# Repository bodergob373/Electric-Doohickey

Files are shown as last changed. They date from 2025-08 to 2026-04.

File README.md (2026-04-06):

# Electric-Doohickey

## Description
A custom go-kart powered by 6 Nissan Leaf battery modules in series. It is driven by two hoverboard motors. The throttle sends signals to a microcontroller, which sends adjusted signals to both motor controllers. The rear wheels are on a suspension arm 

## Why?
My main goal for the future is to build an ethanol-electric hybrid car from scratch. To do this, I need real-world experience designing electrical and mechanical stuff and more practice welding. I'm making this project so that I can design the electric part of the hybrid car and test it on a small, fast, and fun vehicle with only half the number of batteries, motor controllers, and motors.

## The Build
https://github.com/user-attachments/assets/639fb712-8df2-44af-8d2e-14ca03924510





## Model




## Wiring Diagram


### 3D Printed Parts for Mounting the Twist Throttle and Hoverboard Motor


### Hoverboard Motor Connected with 3D-Printed Mount


### BOM:

| Part | Purpose | Amount | Cost |
|---|---|---|---|
| Curved and straight metal tubes | Frame | 4 curved, 6 straight | $0.00  |
| Extension springs | Rear suspension | 4 | $0.00  |
| Plastic chair | Seat | 1 | $0.00  |
| 10" tires | Front wheel and stabilizers | 3 | $0.00  |
| Hoverboard motor | Rear wheels | 2 | $0.00  |
| ESP32 | Send throttle input to both controllers | 1 | $0.00  |
| 2S LiPo battery | Power microcontroller and contactor | 1 | $0.00  |
| Switch | Connect small battery to microcontroller and contactor | 1 | $0.00  |
| 3/4" x 24" threaded rod | Hold suspension arm | 1 | $10.51 |
| 5/16" x 72" threaded rod | Hold battery modules | 1 | $7.57  |
| 5/8" x 12" threaded rod | Hold front wheel and springs | 1 | $4.34  |
| 5/8" x 36" threaded rod | Axle for stabilizing wheels | 1 | $11.31 |
| 1/2" x 36" threaded rod | Steering rod | 1 | $7.93  |
| Used 2nd-gen Nissan Leaf battery modules | Power motors | 6 | $80.00 |
| Twist throttle | Throttle | 1 | $4.94  |
| Motor controllers | Control motors | 2 | $120.00|
| 135A contactor | Connect battery to motor controllers when turned on | 1 | $14.29 |
| 0.25" x 1" x 72" aluminum flat bar | Bus-bars for battery power terminals | 2 | $18.72 |
| 20mm M6 bolts | Connect power terminals to bus-bars | 30 | $8.07  |
| 100 ft 20 AWG silicone wire | Connect to throttle and contactor | 100 ft | $13.98 |
| 1/4" ring terminals | Connect to throttle and contactor | 100 | $8.99  |
| 20 ft 8 AWG silicone wire | Connect motor controller to battery and motors | 20 ft | $19.99 |
| 1/2" shaft collars | Hold parts on steering rod | 10 | $8.49  |
| 5/8" shaft collars | Hold wheel nuts in place | 10 | $8.49  |
| 3/4" shaft collars | Hold suspension arm in place | 8 | $13.99 |
| Misc screws, nuts, and washers | Attach wheels, springs, steering, throttle  | ~20 | $10.00 |
| | **Total** | | **$371.61** |

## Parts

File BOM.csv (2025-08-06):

Part | Purpose | Amount | Cost | Notes
curved and straight metal tubes | frame | 4 curved, 6 straight | 0 | scrap trampoline parts
extension springs | rear suspension | 4 | 0 | scrap trampoline parts
plastic chair | seat | 1 | 0 | already have
10" tires | front wheel and stabilizers | 3 | 0 | already have
hoverboard motor | rear wheels | 2 | 0 | already have
esp32 | send throttle input to both controllers | 1 | 0 | already have
2s lipo battery | power microcontroller and contactor | 1 | 0 | already have
switch | connect small battery to microcontroller and contactor | 1 | 0 | already have
3/4" x 24" threaded rod | hold suspension arm | 1 | 10.51
5/16" x 72" threaded rod | hold battery modules | 1 | 7.57
5/8" x 12" threaded rod | hold front wheel and springs | 1 | 4.34
5/8" x 36" threaded rod | axle for stabilizing wheels | 1 | 11.31
1/2" x 36" threaded rod | steering rod | 1 | 7.93
used 2nd-gen nissan leaf battery modules | power motors | 6 | 80 | 30 modules were $400
twist throttle | throttle | 1 | 4.94
motor controllers | control motors | 2 | 120 | i've already bought the more expensive motor controllers for the old design. this is the price of the cheaper motor controllers i would have used for the new design.
135A contactor | connect battery to motor controllers when turned on | 1 | 14.29
0.25"x1"x72" aluminum flat bar | bus-bars for battery power terminals | 2 | 18.72
20mm m6 bolts | connect power terminals to bus-bars | 30 | 8.07
100 ft 20 AWG silicone wire | connect to throttle and contactor | 100 ft | 13.98
1/4" ring terminals | connect to throttle and contactor | 100 | 8.99
20 ft 8 AWG silicone wire | connect motor controller to battery and motors | 20 ft | 19.99
1/2" shaft collars | hold parts on steering rod | 10 | 8.49
5/8" shaft collars | hold wheel nuts in place | 10 | 8.49
3/4" shaft collars | hold suspension arm in place | 8 | 13.99
misc screws, nuts, and washers | attach wheels, springs, steering, throttle | ~20 | 10
 |  |  | Total
 |  |  | 371.61

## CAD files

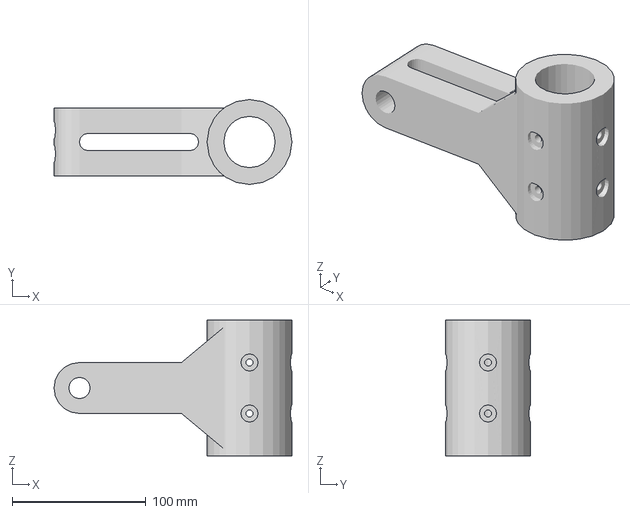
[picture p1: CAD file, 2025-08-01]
CAD/wheelmountprint.step
177.8 x 63.5 x 101.6 mm

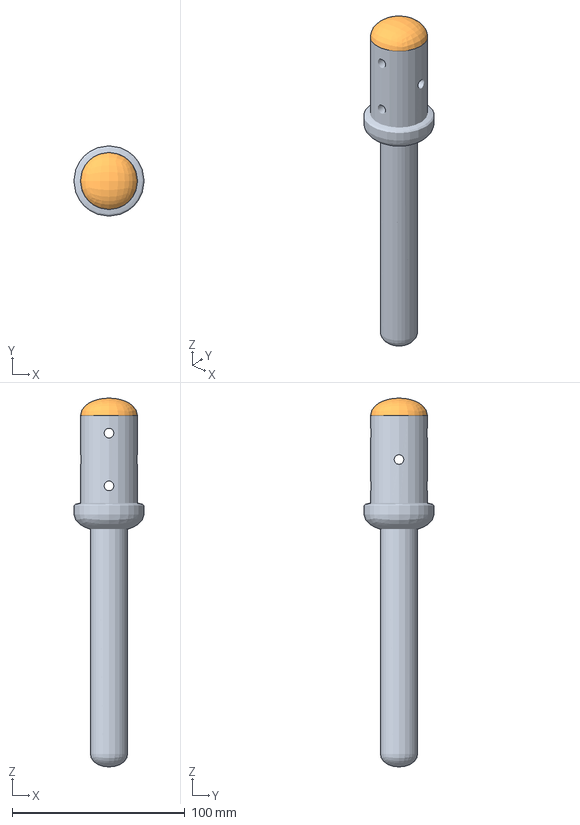
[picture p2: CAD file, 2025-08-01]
CAD/handlemountprint.step
40.6 x 40.6 x 213.4 mm

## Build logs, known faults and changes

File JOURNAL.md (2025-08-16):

---
title: Electric Doohickey
author: Jonathan Itoh
description: A custom go-kart powered by 6 Nissan Leaf battery modules. It is driven by two hoverboard motors. The throttle sends signals to a microcontroller, which sends adjusted signals to both motor controllers. The rear wheels are on a suspension arm.
created_at: 2025-06-25
---
**total time spent: 130h**

# June 25th: Research
In order to use one of the 12kW 72V hub motors that I want to use for the full car, I need powerful batteries. I looked at battery cells to buy, but I would need a lot of them. They're expensive and I don't want to wire them all together, so I searched for used EV/hybrid batteries. I found listings for battery modules from both a Toyota Prius and Nissan Leaf. I decided to use the Leaf batteries because they're cheaper and more commonly used.

module-from-nissan-leaf-gen-2-24kwh

**Total time spent: 4h**

# June 26th: Research 2
I thought that because they're from a car, maybe I could only use one module with smaller motors. After researching the nominal voltage, I would need more because they're only 8.4V. If I want to keep using the powerful motor, I would need 9 modules. It turns out that their nominal voltage is around 7.2V, so I would actually need 10 in series. The battery also needs to supply enough current for the motor. 12000kW / 72V is 167A, so I will need more battery modules in parallel. I chose to have 4 modules in parallel for the full car with 2 motors, so this kart with only 1 motor should only have 2 in parallel. It's still not enough to run at 12kW continuously, but it could maybe supply enough for a few seconds during acceleration.



**Total time spent: 3h**

# June 28th: Research 3
I found the motor controller. It's liquid-cooled and can handle 150A continuous at 72V. I researched parts of a liquid cooling system, but I realized it probably won't be using too much continuous current.

**Total time spent: 3h**

# June 28th: Batteries
I bought 30 Nissan Leaf batteries and made sure they worked.



**Total time spent: 3h**

# July 1st: Metal
I looked around for scrap pipes and found curved segments of an old trampoline frame. I tore it apart, measured the segments, set up the 3D workspace, and modeled them. I had a hard time modeling the curve so I measured the pipe's length, made a circle with a circumference 12 times that, and got a 12th segment. Because they're curved, an oval frame would be simple.



**Total time spent: 5h**

# July 2nd: Designing
I measured parts the 10" wheels and modeled them. I also got their inner diameter and found that Home Depot had perfect 5/8" threaded rods. Then, I measured the battery modules, double checked them with online dimensions, and modeled them. I looked at how batteries are usually wired in series and parallel and made the 10S2p design with the battery modules.



**Total time spent: 3h**

# July 3rd: Designing 2
Using bus bars that go across the batteries in a straight line would be simpler, so I rotated every other parallel group and added bus bars. For the kart, I decided to use 4 curved segments in an oval. For simplicity, the steering is only 1 wheel. It's not a bike so I put the other wheels on the sides to keep it upright. I designed the fork, arranged the frame quarters, positioned the seat and steering, added foot bars, designed the battery frame, and put the side wheels at an angle.




**Total time spent: 4h**

# July 4th: Research 4
Found crimp terminals for connecting the motor to the motor controller. I started researching what BMS I need. Only one voltage-sensing lead is needed per parallel group, so I would need a 10S BMS that can handle high amps. Many people use Orion BMS, but they're $400-$800. I spent a while lookimg for BMS units on Aliexpress and couldn't find many. I also wasn't completely sure whether I actually need only one for the whole battery pack or one per series string. The only one I found that might work could be an ANT BMS.

ANT-BMS-10S-24S-50A-180A-Smart-32V-88V-Lifepo4-li-ion-LTO-Battery-Protection-Board-Double-PCBA-2
71Gar08qu2L _SX522_

**Total time spent: 5h**

# July 5th: Research 5
I realized that the Nissan Leaf modules each have 4 cells in a 2S2P configuration, so a 10S BMS wouldn't even work well. I also found out that the mysterious third terminal between the positive and negative terminals is due to the 2S and is required for voltage sensing. So instead, I will need a 20S BMS. I searched Aliexpress again and found a company that has many different BMS units and found a 25S BMS. I went back to Aliexpress and searched for the same model and found a slightly cheaper one. The BMS requires outside charge, discharge, and pre-charge contactors. I found a 500A contactor.

**Total time spent: 4h**

# July 6th: Research 6
Apparently, another motor controller from the same company is both better and $60 cheaper than the one I already found, so I will use that. The pre-charge contactor does not need to handle as much current, so I found a smaller and cheaper contactor. The 500A contactors I found disappeared so I will use ones that the BMS seller also has. The wiring diagram in the BMS manual also shows that a pre-charge resitor is needed. I calculated the required resistance and found a chassis-mount resistor that can handle the current. I also calculated the cross-sectional area of copper I need for the bus bars on the positive and negative terminals. The bus bars for the voltage-sensing terminals only need to be cheap and wide enough to bolt onto the terminals. I was able to find enough copper at good sizes for a decent price. Then, I found M4 and M6 brass bolts and screws for the battery terminals. For wiring, I found 20 AWG silicone wire for voltage sensing and 8 AWG silicone wire for the motor controller. 2/0 AWG silicone wire is way too expensive.





**Total time spent: 6h**

# July 7th: Designing 3
I modeled the motor controller.



**Total time spent: 0.5h**

# July 9th: Designing 4
To simplify battery mounting and wiring, I put all the batteries in one stack supported by threaded rods on three crosspipes of the frame. I also modeled the BMS, shunt resistor, both contactor sizes, the hub motor, and the twist throttle. To fit the twist throttle to the pipe, I designed a 3D printable adapter that it could fit around. Then, I added angled pipes to connect the stabilizers to the frame. For the rear wheel, I would need a strong way to mount the hub motor on the frame, but that would result in gross angles between the mounting pipes and the curved sides of the frame. I used this as an opportunity to add a swing arm with nice 90 degree angles connected to the frame with a threaded rod, holes, and nuts. For suspension, I put leftover trampoline extension springs under the swing arm so that they would stretch when the suspension is compressed. Finally, I started the wiring design by connecting the motor controller to the hub motor.





**Total time spent: 9h**

# July 10th: Designing 5
I modeled the pre-charge resistor and designed all the wiring. To strengthen the stabilizers and make them easier to build, I removed their tilt and put them both on a threaded rod. I also designed the steering to actually work by havoing a pipe that rotates inside another and supports the lower half of the fork. A threaded rod connects it to the handle with nuts and shaft collars. Because I can't buy the $700 hub motor now, I want to use a hoverboard wheel temporarily because the voltage and current limits of the motor controller can be set. So that I can keep all the metal parts the same, I designed a 3D printable mount that allows the hoverboard wheel to be attached to the swing arm lower down. 





**Total time spent: 7h**

# July 11th: Part Sourcing
I continued looking for parts such as wires and terminals. I would need 2/0 or 1/0 AWG silicone wire to handle the battery amps but it's like $7 per foot. I researched low-cost conductors and found that solid aluminum bars are cheap and lightweight with the only drawbacks of size and flexibility. I replaced the copper bus-bars in my design with slightly thicker and wider aluminum bars and found the right sizes online, saving $20. I still want to eliminate all thick wiring for other parts in the final design.



**Total time spent: 2h**

# July 15th: Final Design
To replace all 2/0 AWG silicone wiring with solid aluminum, I extended the ends of the bus-bars and put the contactors and resistors on them. 



mrbeast for scale



**Total time spent: 2h**

# July 16th: Wiring Diagram
Made the wiring diagram in Google Drawings



**Total time spent: 3h**

# July 17th: BOM
Made the BOM in Google Sheets



**Total time spent: 2h**

# July 21st: Metal 2
Moved all the metal pipes into the garage, then scrubbed and hosed them down. Then, I bought the threaded rods, nuts, and washers from Home Depot.



**Total time spent: 5h**

# July 22nd: Cutting
Because I have a limited number of straight short tubes and longer straight ones were slightly bent, I planned out what pipes will be cut and where. Before I will start cutting them, I laid the main frame quarters together and confirmed the dimensions. Then, I cut off the ends of them so that they could be easily be connected and be stronger.



**Total time spent: 4h**

# August 3rd: Redesign
Redesigned and simplified the wiring and model. Added another hoverboard wheel and reduced the number of batteries to 6.



**Total time spent: 2h**

# August 4th: Cutting 2
Cut all these pipes and made all the holes with a pipe notcher, drill, and angle grinder.



**Total time spent: 7h**

# August 5th: Welding (images from after assembling)
Welded the main curved frame pipes together



Welded the middle crossbeam



Welded the rear swing arm



Welded the frame for mounting the seat



Welded the front fork



**Total time spent: 6h**

# August 6th: Welding 2
Welded the rear crossbeam



Welded the front crossbeam



Welded the frame for the seat to the vehicle frame with short pipes between



Welded the front footrest and front fork mount



Welded a pipe for reinforcing the fork's connection



**Total time spent: 9h**

# August 7th: Assembling

Attached the handlebar pipe and twist throttle mount



Attached the two middle wheels



Fully bolted on the front fork and wheel. It took a while to keep everything aligned while attaching. It wasn't strong enough so I had to weld the pipes of the fork to the threaded rod.



Attached the rear swing arm



Finished assembly:




**Total time spent: 6h**

# August 10th: Electronics

I put the battery modules on the threaded rods and measured the distance between terminals. I marked the aluminum bars, drilled holes, then cut the bus bars off. I did the same for the long bars that carry power to the back. I bolted on the bars and tested their voltage. The entire battery pack was 48V. To make installation safer, I surrounded each long bar with cardboard, added a plastic bar between for support, and covered the rest of the terminals and bus bars with cardboard.




**Total time spent: 4h**

# August 11th: Electronics 2

I attached the hoverboard motor to a controller for testing. They're VESCs, so I downloaded VESC Tool and watched some tutorials on how to use it. I powered the controller and tested different settings. The motor wouldn't spin, but the problem was actually the temporary taped connections for the hall sensors. After crimping them into plugs and soldering them, my settings worked and the motors spun. I also crimped the larger terminals onto the controller and added longer phase wires between the controller and motor.

**Total time spent: 6h**

# August 12th: Electronics 3

Now that the motor controllers and motors work, I need to make the throttle and contactor work. I originally thought I needed a microcontroller to split the throttle signals to the two controllers and to tune them well. I decided to remove the microcontroller because I tested connecting the GND and signal wires to both controllers and powering it from one and it worked. VESC app settings also allowed me to tune the duty cycle based on the minimum and maximum signals from the twist throttle. I measured the car, cut some long wires for the throttle, soldered them, and crimped them onto plugs. I cut some thicker wire, stripped the ends, crimped them onto terminals, and connected them to the motor controller and contactor. Finally, I soldered more long wires to a switch and the contactor so that power can be connected and disconnected.


image (3)

**Total time spent: 7h**

# August 13th: Assembling 2

I lifted the battery onto the frame and connected them with threaded rods. I attached the seat and hoverboard motors, then taped the motor controllers on and started connecting terminals to a small battery for testing. I inverted the direction of one motor and readjusted voltage and current settings. I turned it on and it moved when I twisted the throttle, but one 3D printed wheel mount with less walls snapped. I melted it back together with scrap PLA and a heatgun and it became much stronger. When I brought it outside to test, it stopped turning on because the contactor wouldn't close when I power it.

**Total time spent: 5h**

# August 14th: Final Build

I found out that some wires between the switch and contactor were severed. I connected the small battery plug to the contactor instead and it worked again. I disconnected the hoverboard battery and connected the power terminals to the battery pack and lowered the current limits on the motors to be safe. It still seemed underpowered even after increasing the current max, but I pumped up the tires for less rolling resistance and increased the limits even more and I could drive it.





**Total time spent: 4h**
